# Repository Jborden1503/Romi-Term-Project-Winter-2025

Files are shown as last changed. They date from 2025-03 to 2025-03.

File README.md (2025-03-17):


# Romi 
### Winter 2025
Project by Jake Borden and Ashford Connor 

**Table of contents:**
 - [Romi Design](#romi-design)
   - [Project Description](#project-description)
   - [Hardware Design](#hardware-design)
     - [Physical design](#physical-design)
     - [Bill of Materials](#bill-of-materials)
     - [Wiring Diagram](#wiring-diagram)
 - [Program Design and Structure](#program-design-and-structure)
   - [Tasks](#tasks)
   - [Classes](#classes)
 - [Discussion](#discussion)
 - [Video Demonstration](#video-demonstration)

## Project Description
The Romi robot is based on the ‘Romi’ chassis and motor kit from Pololu robotics. This platform includes a plastic chassis, power distribution board, 2 gearbox and motor combinations, two drive wheels and two caster wheels. Romi is capable of differential, forward and reverse driving, but is incapable of holonomic motion.  Other required hardware includes a pair of encoders, an STM 32L476RG Nucleo board and the proprietary Cal Poly made Shoe of Brian. This constructs a basic ground vehicle capable of driving until the 6 NiMh batteries lose charge, controllable using only encoder feedback. To perform more complicated functions within the scope of this project we added the following sensors and hardware: a 9DOF IMU, 8 x 13 IR reflectance sensor array, and voltage divider circuit. A summary table of all hardware and sensors used can be found below in Table 1.

The robot was tasked with completed the course shown below in Figure 3. There were several different approaches used to complete this course. What follows is our approach to solving this problem, complete with our successes, failures, insights and future steps for improving our Romi. 

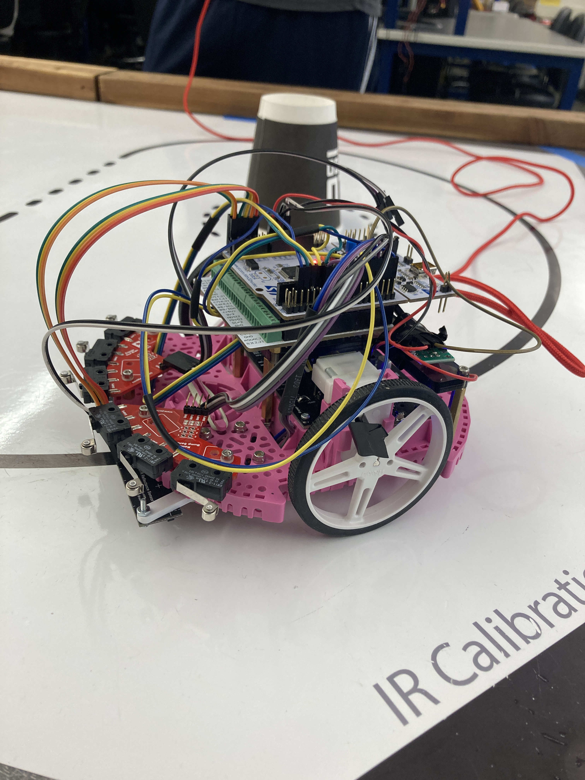
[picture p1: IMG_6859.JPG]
Romi! Romi

###### Figure 1. Assembled Romi.

## Hardware Design
For its attempts to complete the course, Romi had the help of a number of sensors. First, an Adafruit BNO055 IMU was used to keep track of headings. This was connected to the Nucleo using I2C connection. Second, a pair of Pololu bump sensors were used for detecting the wall at the end of the course. Third, a Pololu analog IR reflectance sensor was used for line following. We purchased a sensor with a total of 13 channels, but only ended up using 7 of them for simplicity.

### Physical Design
In order to accomodate the large size of our Line sensor, two additional brackets were 3D printed.
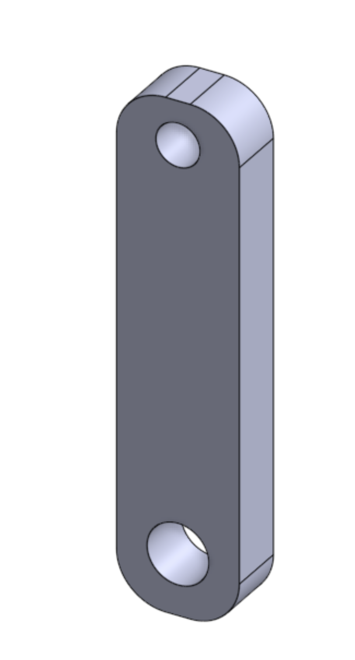
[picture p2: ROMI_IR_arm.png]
IR_ARM! Romi IR Arm

###### Figure 2. Manufactured IR sensor Brace.

### Bill of Materials
##### Table 1. BOM for Romi Project

| Item No. | Description | Supplier | Supplier PN |
|---|---|---|---|
| 1 | Romi Chassis kit (pink) | Pololu | 3501 |
| 2 | Encoder kit | Pololu | 3542 |
| 3 | 8 x 13 analog IR sensor array | Pololu | 4253 |
| 4 | BN055 IMU and breakout board | Adafruit | 2472 |
| 5 | STM 32L476RG Nucleo | ST Microelectronics | STM32L476RG |
| 6 | Shoe of Brian | Cal Poly Mechanical Engineering | N/A |
| 7 | Dupont connectors | Amazon | N/A |
| 8 | 3.3k ohm resistors | N/A | N/A |
| 9 | Perfboard | N/A | N/A |
| 10 | 6 NiMh AA batteries | Amazon | N/A |

### Wiring Diagram
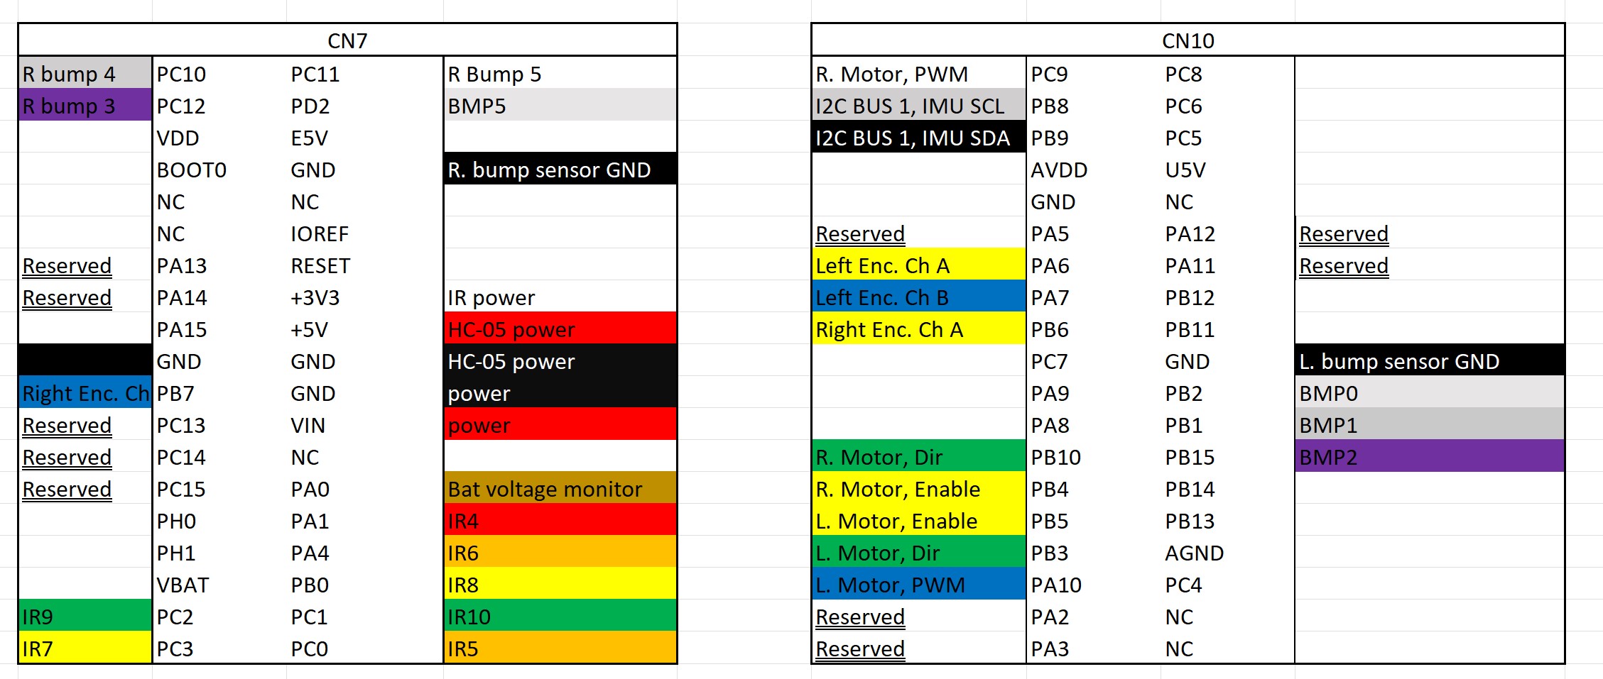
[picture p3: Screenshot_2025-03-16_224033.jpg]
Pinout! Pinout


## Program Design and Structure

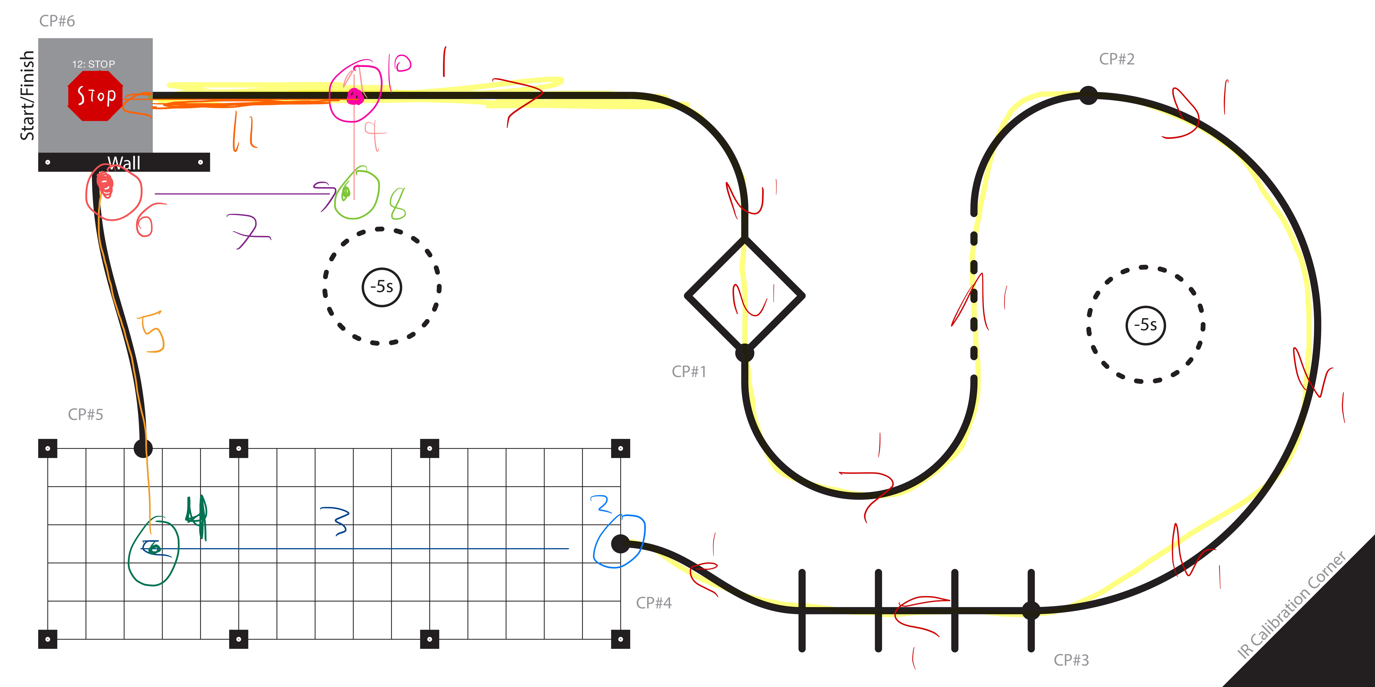
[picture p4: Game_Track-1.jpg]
Game Track! Game Track With States

###### Figure 3. Game track showing location of states. 

### Tasks
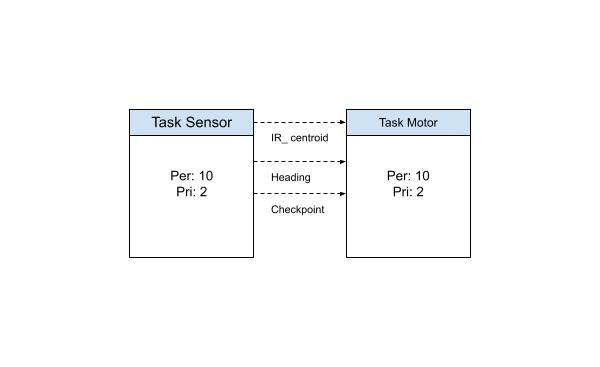
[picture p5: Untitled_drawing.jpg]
Taskdia! Tasking diagram

###### Figure 4. Task Diagram.
#### Sensor Task

The sensor task is responsible for reading sensor values and keeping track of significant milestones on the course. This task is functionally similar to a mastermind task, but it differs chiefly by its direct interaction with external hardware. Given the simple nature of checking course progress, it was appropriate to roll this function into the sensor task to improve memory consumption. This task is run with a priority of 2 and a period of 10 ms.

The task takes an encoder object, an IR sensor object, and an IMU object. It communicates with the motor task using three shares: the centroid share, the heading share, and the checkpoint share.

- The **centroid share** is used to share the value of the centroid as computed in the sensor task. The sensor task will only put values into this share and does not need to get them out.
- The **heading share** is used to share the value of the heading as computed in the sensor task. This will be shared as a -179-0-180 degree value, while the sensor task itself uses the raw 360-degree reading to determine the robot's true orientation. This is done because it is more useful to the PID controllers in the motor task. The sensor task will only put values into this share and does not need to get them out.
- The **checkpoint share** is used as a flag to tell the motor task that it has reached the end of its current state. When the sensor task determines that the state is finished, using sensor data, a 1 is placed in the checkpoint share. The sensor task will only put a value of 1 into this share and does not read the value.

There are **12 states** in the sensor task. The transitions are determined using either encoder positions or heading angles. When the sensor value falls within the specified range, the state is considered finished, and the sensor task signals the transition using the checkpoint share and setting its own internal state variable to the next state.

The initialization of this task is done inside a run-once `if` statement above the while loop of the main generator function. This looks for a global variable called `sensor_init`, which the main function sets to `True` before starting the scheduler. Once init functions are complete, `sensor_init` is set to `False` so that the init functions will not run again. A more elegant and Pythonic implementation of this code would be to implement the task as a class, where the init functions are performed automatically upon instantiation of a sensor task object.

##### State Descriptions
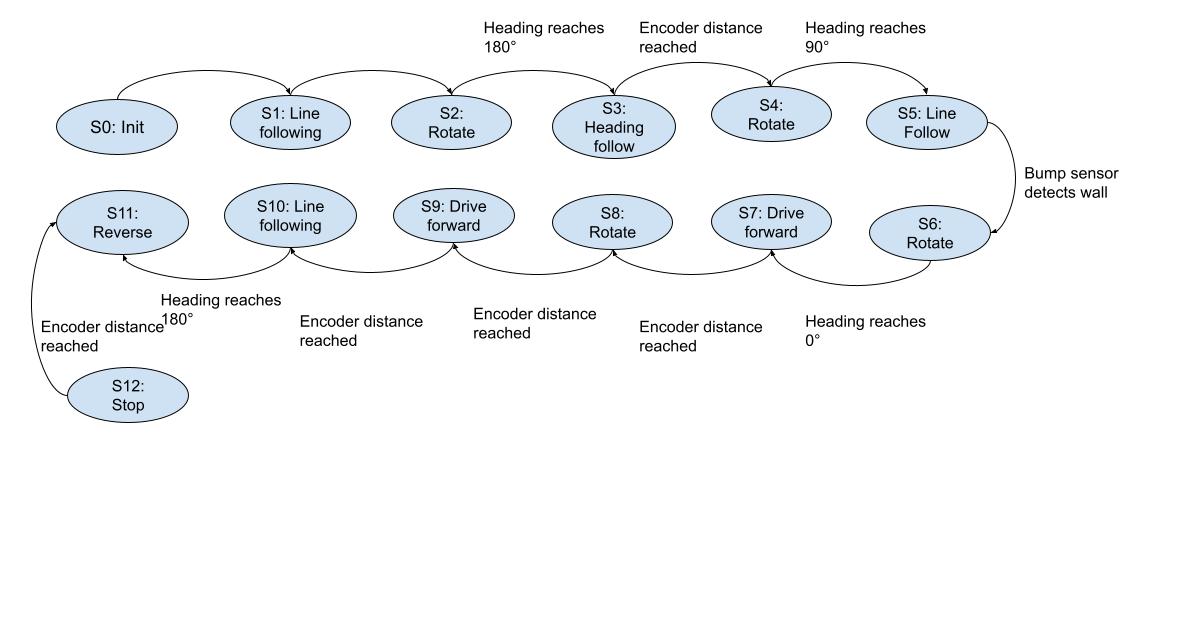
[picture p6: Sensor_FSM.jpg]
Sensor States! Sensor Fsm

###### Figure 5. Sensor FSM.
- **STATE_1**: Line following through the course until checkpoint #4. The sensor task computes the centroid from the IR line sensor and sends it to the motor task via the centroid share. 

- **STATE_2**: Changing the heading of Romi at checkpoint #4. The state reads the raw angle heading, tests it against the desired heading of 180 degrees (with respect to the starting angle), computes the bi-directional angle, and puts it in the heading share. Once the raw angle falls within the desired range, the encoder will be zeroed, a 1 will be put in the checkpoint share, and `sensor_state` is set to `STATE_3`.

- **STATE_3**: Heading following. This state is identical to the previous state, except that the transition point is an encoder distance rather than an angle. This state runs between checkpoint #4 and the turning point at the end of the grid. Once the distance to the end of the grid is read by the encoder, the state will zero the encoder, put a 1 in the checkpoint share, and `sensor_state` is set to `STATE_4`.

- **STATE_4**: Identical to `STATE_2`, but with a different final setpoint. It is a turn-in-place state with the only output being the bi-directional heading. The final heading will be 90 degrees with respect to the starting angle. The state transition process is the same.

- **STATE_5**: Nearly identical to `STATE_1`, with the state output being the centroid for line following. The transition out of this state, however, is triggered by the bump sensor. Each pass through this state, the bump sensors' Booleans are checked to see if Romi has encountered the wall. If one of the Booleans is `True`, then the standard state transition will occur as it has in the other states so far.

- **STATE_6**: Identical to `STATE_2`, but with a different final setpoint. It is a turn-in-place state with the only output being the bi-directional heading. This state is used to turn in place in preparation to drive around the wall. The final heading will be 0 degrees with respect to the starting angle. The state transition process is the same.

- **STATE_7**: Identical to `STATE_3`, but with a different final setpoint. It is a heading-following state with the only output being the bi-directional heading. The heading will be 0 degrees with respect to the starting angle. The state transition process is the same and will be triggered by reaching the desired encoder distance in millimeters.

- **STATE_8**: Identical to `STATE_2`, but with a different final setpoint. It is a turn-in-place state with the only output being the bi-directional heading. The final heading will be 90 degrees with respect to the starting angle. This state is used to turn in place towards the line. The state transition process is the same.

- **STATE_9**: Identical to `STATE_3`, but with a different final setpoint. It is a heading-following state with the only output being the bi-directional heading. The heading will be 90 degrees with respect to the starting angle. The state transition process is the same and will be triggered by reaching the desired encoder distance in millimeters when Romi re-joins the line.

- **STATE_10**: Identical to `STATE_2`, but with a different final setpoint. It is a turn-in-place state with the only output being the bi-directional heading. The final heading will be 180 degrees with respect to the starting angle. This state is used to turn in place on the line. The state transition process is the same.

- **STATE_11**: Identical to `STATE_1`, but with a target encoder distance equal to the distance traversed to avoid the wall. This is the final state transition to the stop state, but it follows the same process.

- **STATE_12**: The stop state. This state does nothing.

#### Motor Task 

The Motor Task is responsible for the actuation and control of both of Romi’s motors. It receives a base speed parameter, a gain compensator object for battery voltage correction, two motor objects instantiated from the `Motordriver` class, and seven PID controllers corresponding to various setpoints along the course. Instead of interfacing directly with sensors, the Motor Task relies on sensor data shared by a separate Sensor Task. This shared data includes the IR sensor centroid value for line following, the heading value from the IMU, and a checkpoint signal that communicates state transitions. When the checkpoint share indicates a value of 1, it signifies that a checkpoint has been reached. The Motor Task then resets this share to 0 and updates its internal state variable (motor_state) to proceed to the next state.

Initialization of the Motor Task occurs within a run-once section at the beginning of the main generator function. This section checks for a global variable named `motor_init` (which the main function sets to `True`) and performs all necessary initialization routines. After the initialization is complete, the variable is set to `False` so that the initialization code does not run again. A more Pythonic approach would be to encapsulate the Motor Task within a class, allowing automatic initialization when an object is instantiated.

The task is implemented as a state machine with twelve distinct states, and transitions between states are determined solely by the checkpoint signal provided by the Sensor Task.

##### State Descriptions

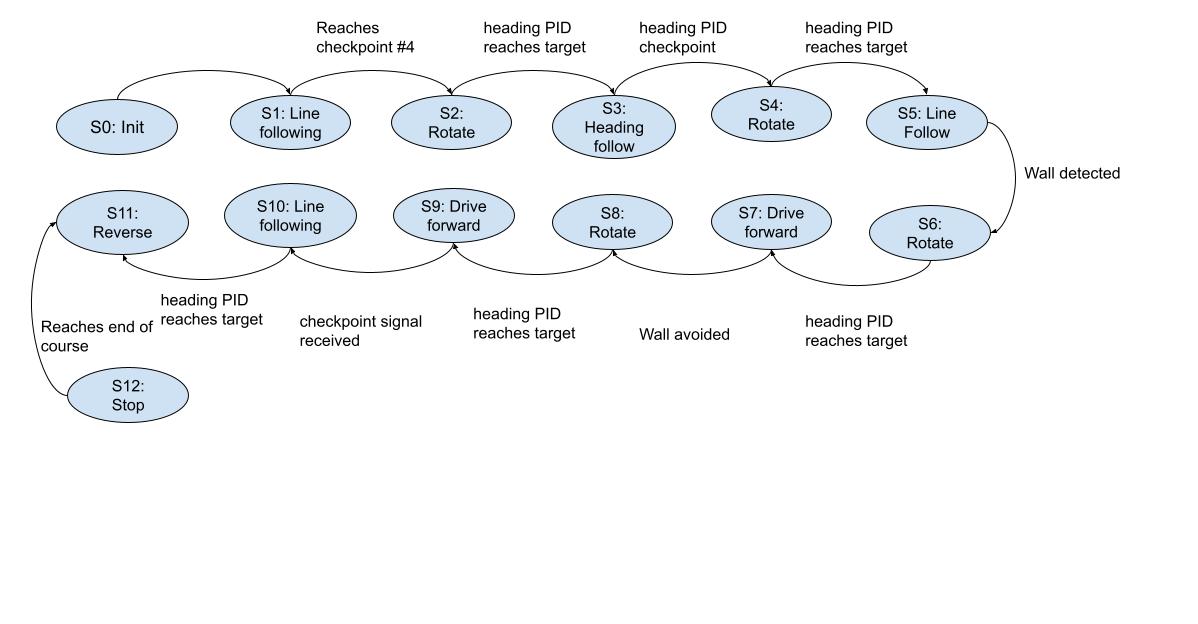
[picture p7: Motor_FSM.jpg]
Motor States! Motor Fsm

###### Figure 6. Motor FSM.
**STATE_1:**  Romi performs line following along the course until it reaches checkpoint #4. In this state, a PID controller processes the centroid value from the IR sensor and computes an actuation value. The computed output is used to adjust the base duty cycle: the left motor receives a command that is the base speed decreased by the corrected PID output, while the right motor receives a command that is the base speed increased by the same corrected value. When the checkpoint share is set to `1`, the system transitions to `STATE_2`.

**STATE_2:** Romi is required to stop and turn in place at checkpoint #4. At the start of this state, both motor efforts are set to zero. A heading PID controller then takes the heading value from the heading share, computes an actuation value, and this value is adjusted for battery charge by the compensator. The left motor is driven with the negative of this corrected output, while the right motor receives the raw corrected output. A checkpoint signal of `1` prompts a transition to `STATE_3`.

**STATE_3:** Romi follows its heading until it reaches the end of the grid. Here, the PID controller uses the heading value to compute an actuation value, and similar to STATE_1, the base duty cycle is modified accordingly: the left motor is given the base speed minus the PID output (after compensation) and the right motor the base speed plus the PID output. When the checkpoint share indicates that a checkpoint has been reached, the task transitions to `STATE_4`.

**STATE_4:** Romi stops and turns in place at the end of the grid. The motors are first set to zero, and then a PID controller processes the heading value to determine an actuation output. After compensation, the left motor is commanded with the negative of the PID output while the right motor receives the unaltered PID output. A checkpoint signal then triggers the transition to `STATE_5`.

**STATE_5:** Romi resumes line following similar to STATE_1, where the robot continues to follow the line until it detects the presence of a wall. Once the Sensor Task signals the wall detection by setting the checkpoint share to `1`, the Motor Task transitions to `STATE_6`.

**STATE_6:** Romi stops and turns in place at the wall. The state begins with both motor efforts set to zero, and a PID controller processes the heading value to compute an actuation value, which is then corrected for battery voltage. The left motor receives the negative of this value, and the right motor receives the raw value. Upon receiving the next checkpoint signal, the task advances to `STATE_7`.

**STATE_7:** Romi performs heading following to avoid the wall. The PID controller processes the heading value to produce an actuation value, and the adjusted base speed is applied to the motors: the left motor gets the base speed decreased by the corrected PID output, and the right motor receives the base speed increased by the same amount. 

**STATE_8:** Romi stops and turns in place past the wall. Similar to previous stop-and-turn states, both motors are set to zero initially; then a PID controller computes an actuation value based on the heading data, the compensator adjusts this value for battery voltage, and the left motor is driven with the negative of the corrected output while the right motor receives the raw output. A checkpoint signal moves the task to `STATE_9`.

**STATE_9:** Romi performs heading following to rejoin the line. The PID controller processes the heading value, and the motors are commanded with the base speed modified by the compensated PID output: the left motor receives the base speed minus the PID output and the right motor receives the base speed plus the PID output. The state transitions to `STATE_10` when a checkpoint signal is received.

In **STATE_10:** Romi stops and turns in place while on the line. Both motor efforts are initially set to zero, and a PID controller uses the heading value to compute an actuation output. After battery compensation, the left motor is commanded with the negative of the PID output and the right motor with the raw output. A checkpoint signal then causes a transition to `STATE_11`.

**STATE_11:** Romi resumes line following until it reaches the end of the course. This state is essentially identical to STATE_1. Once the Sensor Task indicates that the course is complete by setting the checkpoint share to `1`, the Motor Task transitions to the final state, `STATE_12`.

**STATE_12:** Both motors are commanded to stop completely, bringing the robot to a full halt.

Throughout all these states, the actuation commands are computed using the appropriate PID controller and are then adjusted for battery voltage using the compensator. The final motor commands are applied through the `set_effort()` method of the `Motordriver` class. This framework provides a robust control mechanism for navigating the robot through its course, with state transitions managed externally by the Sensor Task via the checkpoint share.

### Classes
* **Encoder:**
  Interfaces with quadrature encoder hardware to track positional changes using timer channels. It maintains internal counters, updating them through the update() method, which handles position increments, decrements, and overflow scenarios. The encoder’s position is accessed via the get_position() method, and can be reset using __zero()__.

* **Motordriver:**
  Provides a motor driver for controlling a Romi robot. It utilizes a hardware timer channel to generate PWM signals for motor speed control while using digital output pins for direction control and enabling/disabling the motor. The __set_effort()__ method accepts an effort value between -100 and 100, setting the PWM duty cycle accordingly and adjusting the motor direction. Additionally, it includes __enable()__ and __disable()__ methods to control the motor's power state. This class takes the pin names for the PWM pin, enable pin and direction pin as well as the timer number and channel for the PWM as inputs for instantiating an object of this class. 

* **IRsensor:**
  Operates an array of IR sensors for line detection and tracking. It measures analog voltage levels and calibrates sensors against defined black and white surface readings through methods __set_black()__ and __set_white()__, and stores the calibration as a .csv file. Line positions are calculated with __read_line()__, and __get_centroid()__ returns a weighted average indicating the line’s relative location. This class is designed to be implemented with an array of 7 sensors and will therefore require 7 ADC pins on the MCU. It takes the 7 pin names as inputs and creates ADC objects of the pyb.ADC class within the __init__ method and compiles them into a list so that the other methods can read the sensor values using for loops. 

* **PID:**
  Implements feedback control to regulate system performance, reducing errors between measured values and setpoints. The __update()__ method computes proportional, integral, and derivative terms over time to generate an output that effectively corrects system behavior. A controller object of this class can be implemented with any task or state. It does not require motor or sensor objects. It instead takes Kp, Ki and Kd gains as well as an arbitrary setpoint.

* **Gain_compensator:**
  Adjusts motor control outputs based on real-time battery voltage readings to maintain consistent performance. By measuring battery voltage with an ADC pin, it uses __correct_value()__ to scale the motor effort, compensating for the loss of charge that will affect motor performace. This became necssarey to avoid needing to tune the controller gains continuosly as the battery level changed. The change in battery level changes the voltage to the motors, meaning more agressive gains were needed as the battery level dropped. This class was paired with a volatage divider circuit that provided a 'pick off point' for the ADC pin to read the volatge. The was accolpished by stepping down the volatge by a factor of three using three resistaors in series to make the volatge safe for the MCU, then multiplying by three inside the method to get the actual charge on the batteries. 

* **IMU:**
  Handles communication with the Bosch BNO055 IMU sensor via the I²C protocol, offering orientation data through Euler angles. Methods such as __get_heading()__, __get_roll()__, and __get_pitch()__ parse raw IMU data into meaningful orientation angles. It includes capabilities for sensor calibration, mode configuration, and normalization of angle measurements to handle continuous rotations. The class takes a single I2C controller object as an input. The I2C controller is an object of the pyb.I2C class built into MicroPython. 

* **Bumpsensor:**
  Detects physical collisions using an array of bump-switch inputs configured with internal pull-up resistors. The __get_state()__ method returns a boolean status indicating whether any of the sensors have been triggered, enabling immediate collision response in the robot's control logic. An obejct of this class can accomodate an array of size n switches, allowing for multiple sensors in one object or a larger sensor to be used.

### Discussion
Our Romi robot failed to complete the course on the day of its demo. This was likely due to a combination of sensor reliability issues and inefficient code. The robot was unstable at almost any gain and would leave the course at either the first bend or the diamond. This was a surprise to us, because the previous week it made it all the way to checkpoint 4 smoothly at a base duty cycle of 35% for 5 back-to-back runs.  We did observe some abnormal readings from the line sensor at seemingly random intervals, which may have contributed to the reliability problems, but the main problem was likely overburdened tasks that could not run on time.  Since the demo day we have been able to trim the tasks down to run more efficiently and reduce/eliminate potential instances of tasks not running on time. 

In terms of lessons learned from this project, we have several. The first would be to implement the tasks as classes instead of functions to eliminate the need for global variables and increase the modularity of our code. As previously discussed, the tasks use an init global variable to see if it is the first pass through the task. This would be handled by the __init__ method of the task class. 
The second is that determining an appropriate period for each task is of critical importance. If we were to begin all over again, we would spend time determining what the true period of each task was and set their period accordingly with the scheduler. This would ensure that there are no task latency issues that would be difficult to separate from a more common issue such as insufficient proportional gain for one of the PID controllers. 

A third lesson is to re-design the IR sensor mounts to be longer. The mounts we designed, and 3D printed were slightly too short to adequately accommodate the sensor array and the Dupont connector heads. This resulted in some ‘squishing’ of the connectors, which would occasionally cause them to come loose. 

Another lesson of this project was to keep the main file as basic as possible due to memory constraints. This was the motivation to create a separate file for all of the drivers and import them to main. We did find that this slowed tasked down somewhat, another possible reason for the issues we encountered. Overall, it was required to add the necessary functionality to complete the entire course. 

A success of the project was the use of a voltage divider circuit to measure the battery charge and compensate the effort sent to motor accordingly. This saved a significant amount of time and energy that would have otherwise been wasted adjusting PID gains for every battery level. 

An unexpected success of the project was the use of the larger line sensor. Where some teams struggled to read the smaller line on the track, the larger 8x13 sensor had no issues finding the line and computing a usable centroid. The only lesson from the line sensor would be, as mentioned before, to 3D print longer mounts. We discovered that we only needed 7 sensors to be successful and therefore set up the IR sensor class to accommodate exactly 7. This also freed up additional ADC pins which we could use for functions such as the voltage compensation.
The IMU was notoriously unreliable for many groups. We found that we had no trouble communicating with it and never encountered errors caused by it. We did however find that, despite the same calibration constants being written to the IMU, the heading value found by the magnetometer changed frequently. Whether this was a result of electronics in the room, Romi’s motors or hobby-grade electronics, we are unsure, but it did present challenges for our many states that rely on a heading measurement to execute correctly. To compensate for the issue, we normalized all heading angles to the initial angle by setting the angle upon startup as a reference “0” degrees. 

We purchased an HC-05 Bluetooth transceiver to use for serial communication with the nucleo board. Unfortunately, we could never get it to work. Having functional Bluetooth communication would vastly simplify testing of our code. Having to plug in and re-start putty every time we wanted to do a new test run with new gains or a different speed was annoying to say the least and possibly wasteful of our time if you added up the potential savings. The Bluetooth transceiver was a bit of a black box to us, and arriving without documentation, we could not figure out how to configure it correctly. 

Next steps for this project would be to add a user interface task and get bluetooth working. The user interface task was always planned for this project, but due to time constraints with developing the program, it was never written. That is the reason that the motor and sensor tasks have the same, nonzero priority. We have set the program up for future expansions such as the user task or additional sensors. The user interface task would make debugging much easier and allow for easier testing of Romi.  We also wanted to experiment with the ultrasonic sensor but opted to use a bump sensor for simplicity sake. 

Another step would be to improve the control algorithms. Currently only one control loop is used at a time. To improve performance in the future we would like to implement nested control loops and an independent control loop for each wheel. We would want to control the overall yaw rate of the robot and the velocity of each wheel, which can be extrapolated to a centerline velocity for the robot. We think this is the key to traveling at higher speeds. Unfortunately, due to time constraints we were never able to explore this.

We would also like to address the shortcomings of the way we wrote our PID control class. The static setpoint for any object of this class forces us to make many controllers for the motor class, which is wasteful of memory. We would like to update it to have a dynamic setpoint that could be changed as the program flows between states. This also made it cumbersome to implement nested control, contributing to the decision to stick to single controller design.

### Video Demonstration
Video Demo: https://youtube.com/shorts/W2a5v1ok4oA?feature=share

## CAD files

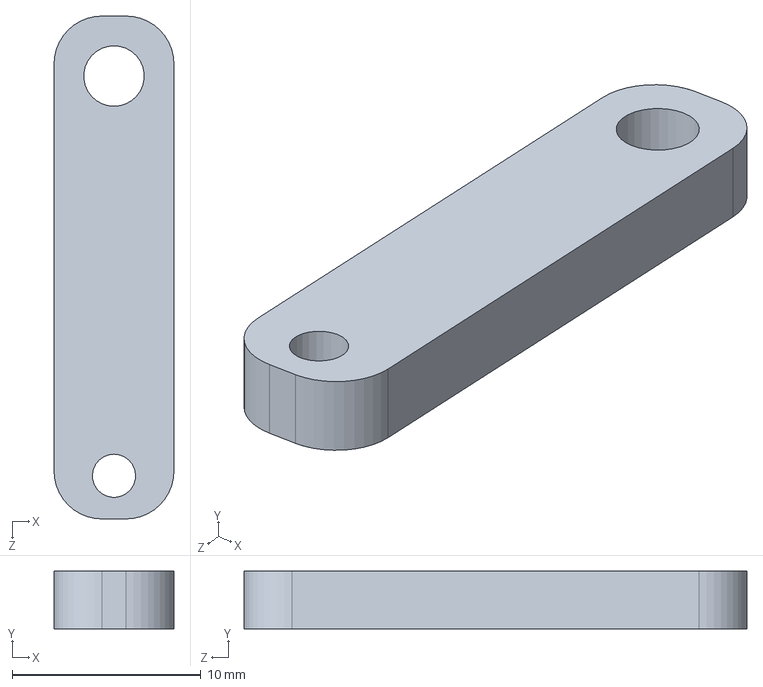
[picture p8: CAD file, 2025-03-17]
romi_IR_arm.SLDPRT
6.35 x 3.05 x 26.6 mm

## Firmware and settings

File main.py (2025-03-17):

## dont delete
from pyb import Pin, Timer, ADC, I2C
from time import ticks_us, ticks_diff, sleep_ms
import cotask
import task_share
from classes import Encoder, Motordriver, IRsensor, IMU, PID, Gain_compensator, Bumpsensor
from os import listdir
from math import pi

STATE_0 = 0
STATE_1 = 1
STATE_2 = 2
STATE_3 = 3
ref_heading = 0.0
checkpoint_heading = 0.0
filelist = listdir()

def rad_to_mm(rads):
    return rads * 35

def wrap_to_180(angle_degs):
    while angle_degs >= 180:
        angle_degs -= 360
    while angle_degs < -180:
        angle_degs += 360
    return angle_degs

# --------------------------------------------------------------------
# Motor Task
#   STATE_1: Line following using pid_line.
#   STATE_2: Rotate using pid_turn (to a setpoint equal to checkpoint_heading - 10°).
#   STATE_3: Stop the motors.
# --------------------------------------------------------------------
def motor_task(shares, left_motor, right_motor, pid_line, pid_turn, base_speed, rotate_speed):
    global motor_init, checkpoint_heading
    if motor_init is True:
        left_motor.enable()
        right_motor.enable()
        compensator = Gain_compensator('PA0')
        motor_state = STATE_1
        motor_init = False

    while True:
        if motor_state == STATE_1:
            # --- LINE FOLLOWING ---
            checkpoint = shares["checkpoint"].get()
            if checkpoint == 1:
                motor_state = STATE_2
                shares["checkpoint"].put(0)
                # Set new target: rotate 10° from the checkpoint heading.
                pid_turn.setpoint = wrap_to_180(checkpoint_heading - 10)
                print("Transitioning to ROTATION state.")
                print("Checkpoint heading =", checkpoint_heading,
                      "New target heading =", pid_turn.setpoint)
            centroid = shares["ir_centroid"].get()
            correction = pid_line.update(centroid)
            correction = compensator.correct_value(correction)
            left_motor.set_effort(base_speed - correction)
            right_motor.set_effort(base_speed + correction)
        elif motor_state == STATE_2:
            # --- ROTATION ---
            current_heading = shares["Heading"].get()  # Expected in [-180, 180)
            correction = pid_turn.update(current_heading)
            correction = compensator.correct_value(correction)
            heading_error = abs(current_heading - pid_turn.setpoint)
            print("Rotating: current =", current_heading,
                  "target =", pid_turn.setpoint,
                  "error =", heading_error)
            if heading_error < 2.0:
                motor_state = STATE_3
                continue
            left_motor.set_effort(correction * rotate_speed)
            right_motor.set_effort(-correction * rotate_speed)
        elif motor_state == STATE_3:
            # --- STOP ---
            left_motor.set_effort(0)
            right_motor.set_effort(0)
        yield 0

# --------------------------------------------------------------------
# Sensor Task
#   STATE_1: Line following – read IR sensor and IMU, compute heading offset relative to ref_heading.
#            When |offset| ≥ 180°, record the checkpoint heading and signal transition.
#   STATE_2: During rotation, update the heading.
#   STATE_3: (Optional) Additional sensor updates if needed.
# --------------------------------------------------------------------
def sensor_task(shares, ir_sensor, imu):
    global sensor_init, ref_heading, checkpoint_heading
    if sensor_init is True:
        sensor_state = STATE_1
        sensor_init = False
    while True:
        if sensor_state == STATE_1:
            ir_sensor.read_line()
            centroid = ir_sensor.get_centroid()
            shares["ir_centroid"].put(centroid)
            imu.read_euler()
            current_heading = imu.get_heading()
            computed_angle = wrap_to_180(imu.compute_angle(current_heading))
            # Compute heading offset relative to the reference.
            angle = wrap_to_180(computed_angle - ref_heading)
            shares["Heading"].put(angle)
            print("Line follow: raw =", current_heading,
                  "computed =", computed_angle,
                  "offset =", angle)
            if abs(angle) >= 180:
                checkpoint_heading = computed_angle
                shares["checkpoint"].put(1)
                sensor_state = STATE_2
                print("Sensor: Reached 180 offset. Checkpoint heading =", checkpoint_heading)
        elif sensor_state == STATE_2:
            imu.read_euler()
            current_heading = imu.get_heading()
            computed_angle = wrap_to_180(imu.compute_angle(current_heading))
            shares["Heading"].put(computed_angle)
            print("Rotation update: raw =", current_heading, "computed =", computed_angle)
        elif sensor_state == STATE_3:
            # Additional sensor state if needed.
            pass
        yield 0

# --------------------------------------------------------------------
# Main Function for State 2
#   - Initializes hardware and calibration.
#   - Creates two PID controllers:
#       pid_line for line following,
#       pid_turn for rotation (setpoint updated during transition).
#   - Starts the sensor and motor tasks.
# --------------------------------------------------------------------
def main_state2():
    global motor_init, sensor_init, ref_heading
    ir_centroid_share = task_share.Share('f', name="ir_centroid")
    heading_share = task_share.Share('f', name="Heading")
    checkpoint_share = task_share.Share('f', name="checkpoint")
    shares = {"ir_centroid": ir_centroid_share, "Heading": heading_share, "checkpoint": checkpoint_share}

    # ----- Hardware Initialization -----
    ir_sensor = IRsensor("PA1", "PC0", "PA4", "PC3", "PB0", "PC2", "PC1")
    ir_sensor.store_cal()
    left_motor = Motordriver(Pin("PA10"), "PB3", "PB5", Timer(1, freq=20000), 3)
    right_motor = Motordriver(Pin("PC9"), "PB10", "PB4", Timer(8, freq=20000), 4)
    controller = I2C(1, I2C.CONTROLLER)
    imu = IMU(controller)
    imu.op_mode('NDOF')
    ref_heading = imu.get_heading()

    if "IMU_cal.txt" in filelist:
        print("Found calibration data, writing constants")
        cal_data = bytearray(22)
        line_num = 1
        with open("IMU_cal.txt", "r") as file:
            for line in file:
                try:
                    stripped = line.strip()
                    values = stripped.split(",")
                    for n in range(len(values)):
                        val = int(values[n])
                        msb = val >> 8
                        lsb = val & 0xFF
                except ValueError:
                    print("Line " + str(line_num) + ", Bad Value")
                except IndexError:
                    print("Index error, idk how")
                else:
                    cal_data.append(msb)
                    cal_data.append(lsb)
                finally:
                    line_num += 1
        imu.write_calibration(cal_data)
    else:
        status = 0
        input("Press enter to calibrate:")
        while True:
            imu_status = imu.cal_status()
            print(f"Status:\n Sys: {imu_status[0]} \nAcc: {imu_status[1]}\nGYR: {imu_status[3]}\nMag: {imu_status[3]}")
            if imu_status[0] == 3:
                print("System Calibrated")
                status += 1
            if imu_status[1] == 3:
                print("Accelerometer Calibrated")
                status += 1
            if imu_status[2] == 3:
                print("Gyroscope Calibrated")
                status += 1
            if imu_status[3] == 3:
                print("Magnetometer Calibrated")
                status += 1
            if status == 4:
                break
            elif status == 3 and imu_status[0] == 0:
                break
            elif imu_status[1] == 3 and imu_status[2] == 3 and imu_status[3] == 3:
                break
            sleep_ms(1000)
        imu.op_mode('CONFIGMODE')
        cal_data = imu.read_calibration()
        filename = "IMU_cal.txt"
        with open(filename, "w") as file:
            file.write(",".join(map(str, cal_data))+"\n")

    imu.op_mode('NDOF')
    ref_heading = imu.get_heading()

    # Create PID controllers:
    desired_centroid = 4.0  # center for line following (for 7-sensor array)
    pid_line = PID(Kp=1, Ki=0.03, Kd=0, setpoint=desired_centroid)
    pid_turn = PID(Kp=1, Ki=0.02, Kd=0, setpoint=0)

    base_speed = float(input("Base Speed: "))
    rotate_speed = 0.2

    L_pins = ['PB2', 'PB1', 'PB15']
    L_bump = Bumpsensor(L_pins)
    R_pins = ['PC12', 'PC10', 'PC11']
    R_bump = Bumpsensor(R_pins)

    encoder = Encoder(Pin("PA6"), Pin("PA7"), 3)
    encoder.zero()

    motor_init = True
    sensor_init = True
    shares["checkpoint"].put(0)
    shares["ir_centroid"].put(4)
    print("FSM: INIT complete. Transitioning to RUN state.")
    sleep_ms(3000)

    sensor = cotask.Task(lambda: sensor_task(shares, ir_sensor, imu),
                           "Sensor_Task", priority=2, period=10)
    motor = cotask.Task(lambda: motor_task(shares, left_motor, right_motor,
                                           pid_line, pid_turn, base_speed, rotate_speed),
                        "Motor_Task", priority=2, period=10)
    cotask.task_list.append(sensor)
    cotask.task_list.append(motor)
    while True:
        try:
            cotask.task_list.pri_sched()
        except KeyboardInterrupt:
            break
    print('\n' + str(cotask.task_list))
    print(task_share.show_all())
    print("State 2 complete.")

if __name__ == '__main__':
    main_state2()

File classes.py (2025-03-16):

from pyb import Pin, Timer, ADC, I2C
from time import ticks_us, ticks_diff, sleep_ms
from os import listdir

class Encoder:
    """
    Encoder driver that updates position on demand.
    """

    def __init__(self, ch_a_pin, ch_b_pin, enc_timer):
        '''@:param ch_a_pin: Type, String. Pin for encoder channel A
        @:param ch_b_pin: Type, String. Pin for encoder channel B
        @:param enc_timer: Type, int. Timer number for encoder '''
        self.timer = Timer(enc_timer, prescaler=0, period=0xFFFF)
        self.ch_a = self.timer.channel(1, pin=ch_a_pin, mode=Timer.ENC_AB)
        self.ch_b = self.timer.channel(2, pin=ch_b_pin, mode=Timer.ENC_AB)
        self.position = 0
        self.current_pos = 0
        self.last_pos = 0
        self.delta = 0

    def update(self):
        '''Updates encoder position. Does not return position'''
        self.last_pos = self.current_pos
        self.current_pos = self.timer.counter()
        self.delta = self.current_pos - self.last_pos
        if self.delta >= 32768:
            self.delta -= 65536
        elif self.delta <= -32768:
            self.delta += 65536
        self.position += self.delta

    def get_position(self):
        ''' Returns encoder position. Must call update method first.'''
        return self.position

    def zero(self):
        '''Sets encoder position and time step to zero.'''
        self.position = 0
        self.current_pos = 0
        self.delta = 0


class Motordriver:
    """A motor driver for Romi."""

    def __init__(self, pwm_pin, dir_pin, enable_pin, timer, channel):
        '''@:param pwm_pin. Type: str. Timer channel pin to be used for PWM output
         @:param dir_pin: Type: str. Pin for motor direction pin
         @:param enable_pin: Type: str. Pin motor enable pin
         @:param timer: Type: int. Timer number for motor PWM
         @:param channel: Type: int. Timer channel for motor PWM'''
        self.dir_pin = Pin(dir_pin, Pin.OUT_PP)
        self.enable_pin = Pin(enable_pin, Pin.OUT_PP)
        self.PWM = timer.channel(channel, mode=Timer.PWM, pin=pwm_pin)

    def set_effort(self, effort):
        '''Sets motor effort in %duty cycle. Saturetion function built into this method. Returns nothing'''
        effort = max(min(effort, 100), -100)
        if effort >= 0:
            self.dir_pin.low()  # forward
            self.PWM.pulse_width_percent(effort)
        else:
            self.dir_pin.high()  # reverse
            self.PWM.pulse_width_percent(-effort)

    def enable(self):
        '''Enables Motor'''
        self.enable_pin.high()

    def disable(self):
        '''Disables motor'''
        self.enable_pin.low()


class IRsensor:
    """
    Driver for an array of 7 analog reflectance sensors.
    """

    def __init__(self, PIN_1, PIN_2, PIN_3, PIN_4, PIN_5, PIN_6, PIN_7):
        '''@:param PIN_1: Type: str. Analog input pin to be used for reading IR sensor values. Sensor #1
        @:param PIN_2: Type: str. Analog input pin to be used for reading IR sensor values. Sensor #2
        @:param PIN_3: Type: str. Analog input pin to be used for reading IR sensor values. Sensor #3
        @:param PIN_4: Type: str. Analog input pin to be used for reading IR sensor values. Sensor #4
        @:param PIN_5: Type: str. Analog input pin to be used for reading IR sensor values. Sensor #5
        @:param PIN_6: Type: str. Analog input pin to be used for reading IR sensor values. Sensor #6
        @:param PIN_7: Type: str. Analog input pin to be used for reading IR sensor values. Sensor #7
        Pins will be configured as ADCs to read analog IR sensor values. '''
        self.pin_1 = Pin(PIN_1, mode=Pin.IN)
        self.pin_2 = Pin(PIN_2, mode=Pin.IN)
        self.pin_3 = Pin(PIN_3, mode=Pin.IN)
        self.pin_4 = Pin(PIN_4, mode=Pin.IN)
        self.pin_5 = Pin(PIN_5, mode=Pin.IN)
        self.pin_6 = Pin(PIN_6, mode=Pin.IN)
        self.pin_7 = Pin(PIN_7, mode=Pin.IN)
        self.adc_list = [
            ADC(self.pin_1), ADC(self.pin_2), ADC(self.pin_3),
            ADC(self.pin_4), ADC(self.pin_5), ADC(self.pin_6), ADC(self.pin_7)
        ]
        self.line_vals = [0] * len(self.adc_list)
        self.black_vals = [0] * len(self.adc_list)
        self.white_vals = [0] * len(self.adc_list)
        self.line_pos_list = [0] * len(self.adc_list)
        self.centroid = 0

    def set_black(self, black_data=None):
        '''This method establishes a datum for 'black' reflectance for each sensor in the array individually. Returns
        a list of integers.'''
        if black_data is None:
            input("Place sensor on BLACK surface and press Enter:")
            for i in range(len(self.adc_list)):
                self.line_vals[i] = self.adc_list[i].read()
                self.black_vals[i] = self.line_vals[i]
                self.line_vals[i] = 0
        else:
            self.black_vals = black_data
        return self.black_vals

    def set_white(self, white_data=None):
        '''This method establishes a datum for 'white' reflectance for each sensor in the array individually. Returns
        a list of integers.'''
        if white_data is None:
            input("Place sensor on WHITE surface and press Enter:")
            for i in range(len(self.adc_list)):
                self.line_vals[i] = self.adc_list[i].read()
                self.white_vals[i] = self.line_vals[i]
                self.line_vals[i] = 0
        else:
            self.white_vals = white_data
        return self.white_vals

    def read_line(self):
        '''This method reads all ADC channels in array and compiles their values into a list. The method also normalizes
        the values to black or white using linear interpolation. Must be called before get_centroid method
         Returns the list of white/black values.'''
        for i in range(len(self.adc_list)):
            self.line_vals[i] = self.adc_list[i].read()
            diff = self.black_vals[i] - self.white_vals[i]
            self.line_pos_list[i] = ((self.line_vals[i] - self.white_vals[i]) / diff) if diff != 0 else 0
        return self.line_pos_list

    def get_centroid(self):
        '''This method takes the list of line values from the read_line method and computes the centroid. Must call
         read_line method first.'''
        total = sum(self.line_pos_list)
        if total != 0:
            self.centroid = sum(val * (i + 1) for i, val in enumerate(self.line_pos_list)) / total
        else:
            self.centroid = 0
        return self.centroid

    def store_cal(self):
        '''Routine for calibrating black and white values from .csv file. Or if no file exists, calibrating and storing
        calibration values in a .csv file.'''
        filelist = listdir()
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
